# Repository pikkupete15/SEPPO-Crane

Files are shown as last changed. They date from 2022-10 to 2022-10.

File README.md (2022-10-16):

# SEPPO-Crane
Aalto-yliopiston tuotesuunnittelukurssin I/2022 ryhmän 2 prototyypin repo. 

<p>Slave kansio - Arduino koodi slave-saksimoduulille</p>
<p>Master kanstio - Arduino koodi master-saksimoduulille</p>
<p>Ohjain kansio - Processing koodi WiFi-ohjaukselle</p>
<p>Elektroniikka - kytkentäkaaviot, diagrammit, osaluettelot, GRBR-tiedostot, levyjen kuvat</p>



Watch the video (https://www.youtube.com/watch?v=MJLLgqbMfsc)

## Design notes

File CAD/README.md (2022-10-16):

CAD: Fusion 360

viewer; https://viewer.autodesk.com/

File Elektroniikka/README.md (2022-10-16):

Täältä löytyy kytkentäkaaviot, BOM, sekä levyjen GRBR-tiedostot. Kaikki levyt suunniteltu jyrsittäväksi yksipuoleisesta 1.6mm pertinax-levystä. 
Folion paksuus 35µm 

Slave- ja Master-laitteiden levyt ovat identtisiä. Ohjelmalla valitaan joko Slave- tai Master-moodi.


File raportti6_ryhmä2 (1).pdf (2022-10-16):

Aalto-yliopisto Insinööritieteiden korkeakoulu

KJR-C2005 Tuotesuunnittelu

Ryhmä: 2. | Päivämäärä: 16.10.2022
Harjoitus: | Viikkoraportti 6
Otsikko: | Loppuraportti ja Gaala

Tekijät:

| Nimi | Opiskelijanr. | PJ vko
1 | Joonatan Rimpiläinen | 790572 | 1
2 | Niko Kuusisto | 1017131 | 2
3 | Petteri Haverinen | 910064 | 3
4 | Aaro Uitto | 910417 | 4

# Tiivistelmä

Tässä ryhmän 2 tuotesuunnittelukurssin (KJR-C2005) loppuraportissa on kerättynä aiempien viikkoraporttien (1–5) keskeiset asiat. Raportissa esitellään ryhmätyönä toteutetun tuotesuunnitteluprosessin eri vaiheet ja niiden lopputulemat, sekä sen kautta valittu ratkaisuvaihtoehto. Valinnan jälkeen ratkaisuvaihtoehtoa kehitettiin ja siitä laadittiin havainnemalli gaalatilaisuutta varten.

Tuotesuunnittelukurssi toteutettiin yhteistyössä Konecranesin kanssa, joka määritteli tuotesuunnitteluprosessin aiheen. Tehtävänantona oli toteuttaa kuorman nosto- /siirtotapahtuma tehdashallissa. Raportissa esiteltyjen järjestelmällisien suunnittelu- ja ideointimenetelmien jälkeen tuotesuunnitteluprosessin tulokseksi muodostui saksimekanismeja hyödyntävä nosturi, joka ei tarvitse tehdashallilta tukevaa seinärakennetta, eikä kiinteää asennusta.

# Johdanto

Teollisissa nostureissa hyvin tyypillinen ratkaisu on jykevä pääkannatin, joka kulkee pitkittäissuunnassa hallin seinien yläosassa olevilla kiskoilla. Pääkannattimen päällä puolestaan ovat toiset kiskot, joiden päällä vaijerinostinkoneisto pääsee kulkemaan. Tämän ns. siltanosturin ehdoton vahvuus on kustannustehokkuuden ja toimintavarmuuden yhdistelmä. Perinteisellä siltanosturilla on myös merkittäviä rajoituksia. Esimerkiksi enimmäisnostokuorma ei riipu pelkästään itse nosturin lujuudesta, vaan myös tehdashallin seinämien kantokyvystä. Siltanosturit voivat myös tilanteesta riippuen hankalia asentaa ja huoltaa, etenkin jos tehdashallin alkuperäisen rakennuksen yhteydessä siltanosturin asennusmahdollisuutta ei ole huomioitu.

Ryhmänä koimme, että siltanosturille ominaiset käyttötilanteet voivatkin olla hyvin suppeita. Kehittyvän teollisuuden maissa olevissa tuotantohalleissa ei ole välttämättä tarpeeksi vahvoja tukirakenteita perinteisen siltanosturin mahdollistamiseksi, mikä hankaloittaa tai jopa estää raskaan laitteiston sijoittamista tai siirtämistä hallin sisällä. Toinen esimerkki voisi olla vaikka erilaiset messuhallit, kuten telttahallit, joissa raskaan kaluston liikkuminen on haastavaa.

Ratkaisumme avulla pyrimme tutkimaan modulaarisempia ja käytännöllisempiä nosturimalleja juuri näihin joustavuutta vaativiin tilanteisiin.

# Menetelmät

Taustatutkimus – Taustatutkimus on jokaisen tuotesuunnitteluhankkeen kannalta yksi tärkeimmistä vaiheista. Tarvittava ratkaisu voi jo olla olemassa, siihen voi kohdistua tiukkoja laki/standardirajoituksia tai tuotteelle ei ole vielä olemassa markkinaa, jolloin tuotteen suunnittelua ei kannatta toteuttaa. Olemassa olevista ratkaisuista voi myös saada inspiraatiota niitä yhdistelemällä tai muokkaamalla.

Tuotesuunnittelutyön tehtävänannon jälkeen teimme laajan taustatutkimuksen, jolla kartoitimme jo olemassa olevia nosturiratkaisuja, niin kirjallisesti kun paikan päällä tutustumalla. Havaitsimme, että tehdashallissa käytettävät nosturit ovat olleet jo lähes 100 vuotta hyvin samanlaisia. Niitä sitovat tiukat ja yksityiskohtaiset standardit, jotka melko suoraan määrittävät, minkälainen nosturin tulee olla.

Vaatimuslista – Vaatimuslista on jokainen hankkeen yksi tärkeimmistä dokumenteista, sillä siihen määritetään ratkaisulta edellytettävät speksit, kuten sen geometria, energianmuoto tai kustannukset, jonka pohjalta varsinainen suunnittelutyö alkaa.

Vaatimuslistaa varten haastattelimme Konecranesin edustajaa Ari Bertulaa luentojen yhteydessä. Vaatimuslistamme piti sisällään 16 erilaista päätunnusta, kuten kinematiikka, voimat, turvallisuus, joihin määriteltiin tarkasti hankkeen toteutuksen kannalta oleelliset asiat.

Abstrahointi – Abstrahointi on menetelmä, jolla saadaan vaatimuslistan oleelliset asiat esille analysoimalla erilaisten toimintojen riippuvuuksia. Abstrahointi pitää sisällään 5 askelta, jotka ohjaavat kriittisesti karsimaan ja muokkaamaan vaatimuslistaa kohti todellista tarvetta.

Abstrahoimme vaatimuslistamme ensin karsimalla kaikki toiveet sekä sellaiset vaatimukset, jotka eivät välittömästi koskeneet toimintaa tai oleellisia ehtoja. Tämän jälkeen jäljelle jääneet määrälliset toteamukset muutettiin laadullisiksi sekä ne supistettiin oleelliseen pitäytyviksi lausumiksi. Jäljelle jääneet vaatimukset lavennettiin yleisemmälle tasolle, joista lopulla muodostettiin ongelma ratkaisuun nähden neutraalisti. Abstrahointiprosessimme lopputulos oli ”Kuorman nostaminen ja siirtäminen tehdashallissa”.

Kokonaistoimintojen jako osiin – Abstrahoinnin tuloksena saadaan ratkaisuun nähden neutraali kokonaistoiminto. Kokonaistoiminto jaetaan pienempiin osatoimintoihin, joka mahdollistaa niiden yksittäisen tarkastelemisen. Osatoimintoihin jako voidaan suorittaa tarkastelemalla kokonaistoiminnon aiheuttamaa muutosta vertaamalla aineen, energian ja signaalin muutosta ennen kokonaistoimintoa ja sen jälkeen.

Pilkoimme kokonaistoiminnon aluksi karkeasti osatoimintoihin ”kuorman nostaminen”, ”kuorman siirtäminen” ja ”kuorman laskeminen”. Jotka tämän jälkeen uudelleen ositimme pienemmiksi kokonaisuuksiksi sisältäen esimerkiksi ”kiinnityksen nostettavaan massaan”, ”voimien välitys hallin rakenteisiin” ja ”nostoliikkeen pysäytys ja lukitus”.

”635” – menetelmä - “635” on ideointimenetelmä, jossa 6 ihmistä ottaa oman tyhjän paperin ja kirjaa sille 3 ideaa ratkaisuksi. Paperi kierrätetään jokaisen ryhmäläisen kautta, niin että jokaisella on 5 minuuttia aikaa jatkojalostaa ja täydentää kyseisen paperin kolmea ratkaisua. Tällä menetelmä saadaan nopeasti erilaista 18 ratkaisuvaihtoehtoa rakennettua.

Käytimme soveltavasti ”635” -menetelmää, sillä ryhmässämme oli vain 4 jäsentä. Saimme menetelmää käyttäen yhteensä 12 ratkaisuvaihtoehtoa, joista muutama olivat hyvin samankaltaisia keskenään. Ratkaisuvaihtoehdoiksi muodostui esimerkiksi ”vaijerinosturi”, jossa 4 erillistä köysinosturia asennetaan tehdashallin kulmiin ja vaijereiden päät niputettaisiin yhteen jonkin pannan avulla.

Aivoriihi - Aivoriihi on ideointimenetelmä, jossa määrä korvaa laadun. Taustalla onkin nimenomaan ajatus, että määrä tuo laatua. Tässä menetelmässä voi heittää huolettomasti hyvinkin epätavallisia ideoita, joista voi ajatusten vaihdossa jalostua toimivia ratkaisuja.

Kun olimme suorittaneet “635”-ideointimenetelmän ja käyneet yhdessä syntyneet ratkaisuvaihtoehdot lävitse, aloimme luonnostaan itse toteuttamaan aivoriihiä ratkaisujen synnyttäneen keskustelun ansiosta. Aivoriihen tuottamia hahmotelmia piirreltiin yhdessä tyhjän luentosalin liitutaululle, joista otettiin valokuvat talteen. Käydystä aivoriihistä syntyi ensimmäinen kipinä lopulliseen toteutukseemme.

Morfologinen laatikko – Morfologiseen laatikkoon listataan jaettujen osatoimintojen mahdolliset ratkaisuvaihtoehdot ja niitä yhdistelemällä eri tavoin saadaan liuta kokonaisratkaisuvaihtoehtoja. Osittaisratkaisuvaihtoehtojen yhdistely voi olla joko satunnaista, tai se voi perustua esimerkiksi siihen, kuinka hyvin eri vaihtoehdot täydentävät toisiaan ja siten sopivat yhteen.

Ratkaisuvaihtoehtojen arvosteleminen painotetuilla kriteereillä

Osittaisratkaisuista kootut kokonaisratkaisuvaihtoehdot arvostellaan esimerkiksi asteikolla 0-10 eri päätunnusten mukaisesti. Tyypillisiä päätunnuksia voivat olla esimerkiksi turvallisuus, ergonomia, valmistus, asennus, kuljetus, käyttö, kunnossapito, kierrätys sekä kustannukset. Jokaiselle päätunnukselle määritetään jokin painotus kokonaisarvioinnissa, jotta tärkeiksi koetut ominaisuudet omaaville ratkaisuille tulee enemmän näkyvyyttä

# Tulokset

Ratkaisun toiminnallinen pienoismalli saatiin toteutettua ja demonstroitua tuotesuunnittelukurssin gaalassa 11.10.2022.

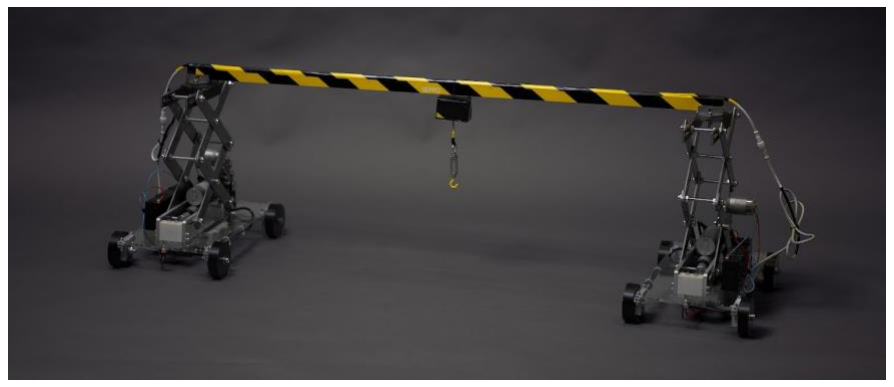
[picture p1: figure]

KUVA 1 VALMIS PROTOTYYPPI NOSTOASENNOSSA

Laitteen prototyypille annettiin nimitys SEPPO. Nimen etymologia tulee Seppo Ilmarisesta sekä ryhmän jäsenen isoisän nimestä.

Laite suunniteltiin Fusion-360 CAD-ohjelmalla ja valmistettiin Aalto Design Factory:n tiloissa. Yhteensä koneistettuja, vesileikattuja, sorvattuja sekä 3D-tulostettuja osia oli 61. Saksipareja päädyttiin tekemään 2 kappaletta. Lisäämällä tai vähentämällä saksipareja, saadaan nostokorkeutta säädettyä standardiosilla. Nostomekanismi on valmis moduuli, joka kulkee pääkannattimella (kuva 1. Musta laatikko pääkannattimen keskellä), joten sitä ei mallinnettu eikä sähköistetty.

Prototyyppi rakentuu kahdesta saksimoduulista, eli pääkannatinta kannattelevista pyörillä kulkevista rakenteista. Molemmat rakenteet sisältävät sähkömoottorin ajamiseen sekä käyttölaitteen saksimekanismin nostamiselle/laskemiselle. Toinen moduuleista on Master-laite, eli sen kautta kulkevat komennot ohjaavat toista moduulia, joka on Slave-laite. Saksimoduulit keskustelevat keskenään UART-väylän kautta. Lisäksi molemmissa moduuleissa on langallinen manuaaliohjaus, eli neljä kytkintä, jotka mahdollistavat moduulin liikkeen eteen-taakse sekä saksimekanismin nostamisen ja laskemisen. Ohjausmekanismia eturenkaille ei prototyyppiin toteutettu.

Elektroniikka kiinnitettiin laitteen pohjaan. Ohjauslevy koteloitiin, mutta H-silta jätettiin avoimeksi kuumenemisen ehkäisemiseksi. Toiminnoista löytyy demovideo (liite 2).

Prototyyppi toimi odotusten mukaisesti – halutut toiminnot saatiin sisäistettyä prototyyppiin. Laitteen toiminta on seuraavanlainen:

1. Saksimoduulit (kuva 1. vasen ja oikea, pääkannattimella yhdistetyt rakenteet) ajetaan käytettävään tilaan pääkannatin käännettynä toisen moduulin suuntaisesti.
2. Toinen saksimoduuli, joka ei kuljeta pääkannatinta ajetaan pääkannatinta kannattavan moduulin viereen.
3. Pääkannattimen satulan kääntölukitus poistetaan ja se käännetään toisen moduulin satulaan kiinni ja lukitaan pultilla (kuva 3 & 4, pääkannattimen alla oleva osa).
4. Toinen moduuli ajetaan etuviistoon ja peruutetaan samalle tasalle, pääkannattimen etäisyyden päähän paikallaan olevasta saksimoduulista.
5. Pyörivät satulamekanismit lukitaan paikalleen.
6. Pääkannatin nostetaan käyttökorkeuteen saksimekanismilla (kuva 4).
7. Laite käyttövalmis (kuva 1).

Molemmat saksimoduulit toimivat itsenäisesti manuaalisella ohjauksella, kun pääkannatinta pitkin kulkeva datalinja ei ole yhdistetty. Kun datalinja yhdistää moduulit, poistuu Slave-moduulin manuaaliohjaus käytöstä, mikä mahdollistaa synkronoidun ohjauksen Master-moduulilta. Manuaaliohjauksen lisäksi laite toimii myös WiFi:n kautta kauko-ohjauksella.

Sulautettu ohjelmisto tehtiin käyttämällä Arduino-kieltä, joka perustuu C ja C++ kieliin. Kaukoohjauksessa käytetty sovellus tehtiin käyttämällä Processing-kieltä. Processing perustuu Javakieleen. WiFi-ohjaus perustuu laitteen ylläpitämään TCP-serveriin, mihin ohjaussovellus liittyy clienttinä lähettäen komentoja, jotka ovat identtisiä UART-komentojen kanssa. Tämä mahdollisti saman string parserin käytön sekä UART-, että WiFi-ohjaukselle.

Kytkentäkaaviot, piirilevyt, koodi sekä CAD-tiedostot löytyvät julkisesta github-reposta (liite 1).

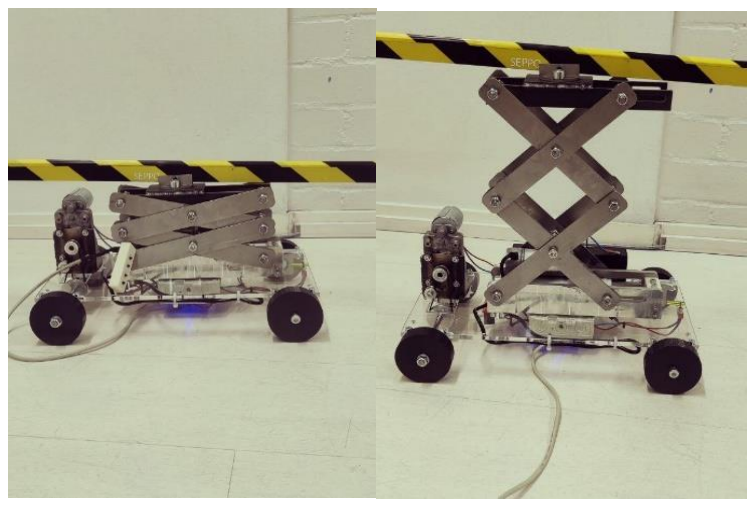
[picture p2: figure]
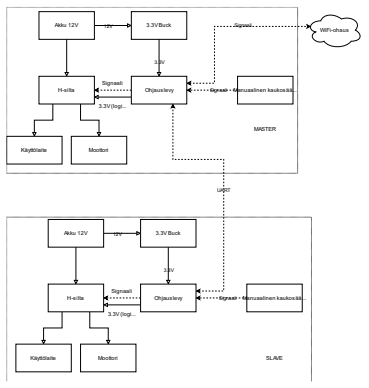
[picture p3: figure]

KUVA 2 ELEKTRONIIKAN OSATOIMINNOT | KUVA 3&4 SAKSIMODUULI ALA- (VAS.) SEKÄ YLÄ-ASENNOSSA (OIK.)

# Pohdinta

Tuotesuunnitteluprosessin tulosten perusteella voidaan sanoa, että uudenlaisen nosturigeometrian luominen on sekä mahdollista että myöskin tarpeellista. Ratkaisumme tuottaa joustavamman ratkaisun epätavallisiin tilanteisiin, joihin perinteinen nosturi ei välttämättä soveltuisi. Lisäksi hinta voi olla perinteistä ratkaisua alempi varsinkin halleissa, joihin ei ole mahdollista asentaa siltanosturia ilman mittavaa remonttia.

Saksinosturi-siltanosturi-hybridiä voitaisiin teollisuussovellusten lisäksi hyödyntää esimerkiksi messuhalleissa, liikkuvuutta ja joustavuutta vaativissa esittelytiloissa, sekä pienillä rakennustyömailla, kuten yksittäisten omakotitalojen rakennuksessa.

Yksittäisen saksinostinelementin sivuttaissuuntaista vakautta ja jykevyyttä olisi syytä käsitellä mahdollisen jatkokehityksen yhteydessä. Saksinostimen lukitusratkaisuja ja niiden suorituskykyä emme käsitelleet tässä prosessissa juurikaan, mikä avaa oven lisätutkimuksille. Lisäksi yksittäiselle nostinelementille voi olla saksinostimen lisäksi myös muita joko varmempia tai kustannustehokkaampia malleja.

Myös pääkannattimeen liittyviä vaihtoehtoja on syytä tutkia, eritoten pääkannattimen ja nostinelementin liitäntää koskien. Pääkannattimen modulaarisuuden ja asennuksen yksinkertaistaminen erilaisten lisäratkaisujen avulla voisi olla myös hyödyllistä

# Tuntikirjanpito

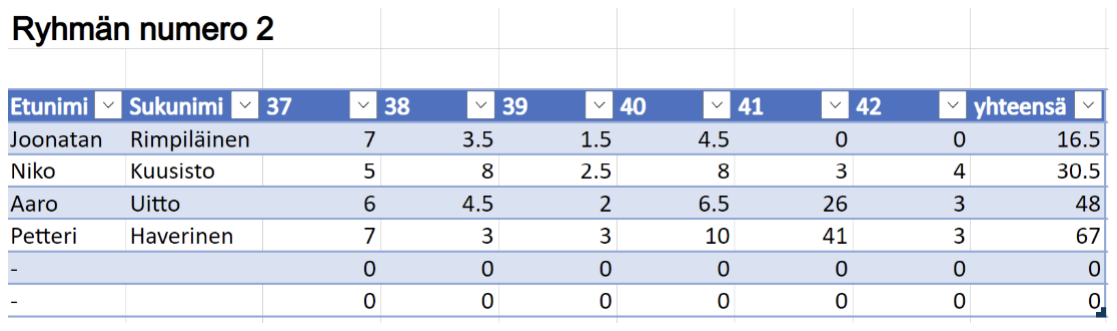
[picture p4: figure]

# Vertaisarviointi

Ryhmän jäsenten mielestä suoriutuminen kurssista oli pääasiassa sujuvaa. Raporteissa onnistuimme parista puutteellisuudesta huolimatta hyvin, ja prosessia seurasimme tarkasti. Havainnemallin toteutukseen olemme hyvin tyytyväisiä, ja prosessin tuottama ratkaisu oli mielestämme looginen. Näiden seikkojen nojalla arvioimme suorituksemme tason riittävän arvosanaan 5.

Tuntikirjanpidossa näkyvät Petteri Haverisen ja Aaro Uiton korkeammat tuntimäärät ovat seurausta prototyypin rakennukseen kuluneesta suuresta ajasta. Jos tämä aika jätettäisiin huomiotta, olisivat tuntimäärät ryhmän jäsenten välillä huomattavasti lähempänä toisiaan.

# Palaute

Kurssin aikana saatu ohjeistus ja tuki oli kattavaa, ja opitun prosessin merkitys ja yksityiskohdat tulivat selkeäksi tavalla, joka on helppo muistaa. Ainoana negatiivisena asiana olisi suunnitteluprosessin aihe, joka oli hieman rajallinen/haastava, mutta tämä ei ole tietenkään kurssin järjestäjien hallinnassa.

Viittaukset ja liitteet

1) Github: https://github.com/pikkupete15/SEPPO-Crane
2) Demonstraatiovideo: https://www.youtube.com/watch?v=MJLLgqbMfsc

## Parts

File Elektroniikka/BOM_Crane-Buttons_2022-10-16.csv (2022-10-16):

ID | Name | Designator | Footprint | Quantity | Manufacturer Part | Manufacturer | Supplier | Supplier Part | Price
1 | HDR-F-2.54_1x5 | H1 | HDR-F-2.54_1X5 | 1 |  |  | LCSC | C50950 | 0.064
2 | K4-6×6_SMD | KEY1,KEY2,KEY3,KEY4 | KEY-SMD_4P-L6.0-W6.0-P3.90-LS10.0 | 4 | K2-6639SP-D4SC-04 | 韩国韩荣 | LCSC | C191626 | 0.052

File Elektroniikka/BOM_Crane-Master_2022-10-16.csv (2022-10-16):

ID | Name | Designator | Footprint | Quantity | Manufacturer Part | Manufacturer | Supplier | Supplier Part | Price
1 | HDR-F-2.54_1x5 | H1 | HDR-F-2.54_1X5 | 1 |  |  | LCSC | C50950 | 0.064
2 | CONN-TH_2P-P5.00 | P1,P2,P3,P5 | CONN-TH_2P-P5.00 | 4 |  |  | LCSC
3 | CONN-TH_3P-P5.00 | P4 | CONN-TH_3P-P5.00 | 1 |  |  | LCSC
4 | 1k | R1,R2,R3,R4 | R1206 | 4
5 | Buck-module | U1 | BUCK-MODULE | 1 |  |  |  | https://www.amazon.com/4-75-23V-1-17V-DC-DC-Converter-Module/dp/B00NJCAI7G
6 | WEMOS-D1-MINI | WEMOS1 | WEMOS-D1-MINI | 1

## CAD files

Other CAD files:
CAD/Tuotesuunnitteluprojekti v25.f3d

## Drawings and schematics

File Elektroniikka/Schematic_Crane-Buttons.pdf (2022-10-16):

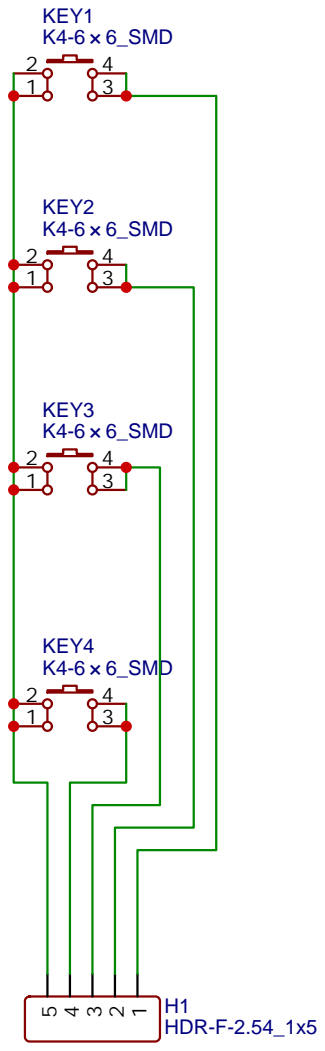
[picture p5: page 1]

Drawn By: Petteri Haverinen

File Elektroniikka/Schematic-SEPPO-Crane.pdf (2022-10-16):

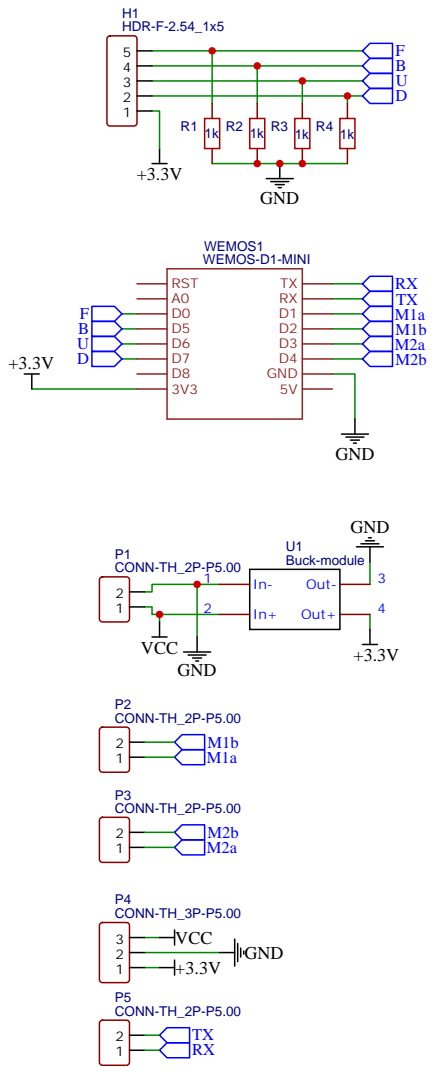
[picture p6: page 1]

Drawn By: Petteri Haverinen

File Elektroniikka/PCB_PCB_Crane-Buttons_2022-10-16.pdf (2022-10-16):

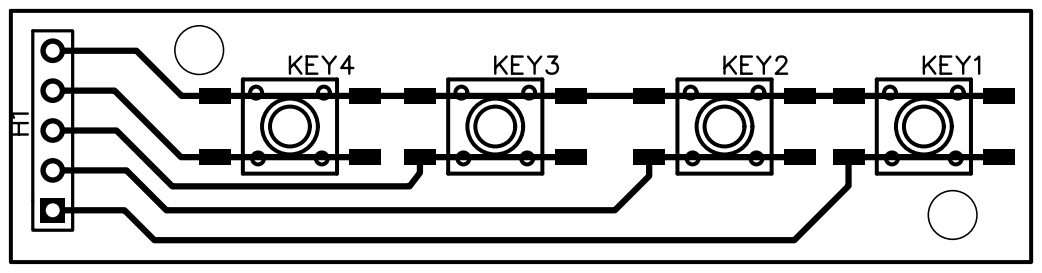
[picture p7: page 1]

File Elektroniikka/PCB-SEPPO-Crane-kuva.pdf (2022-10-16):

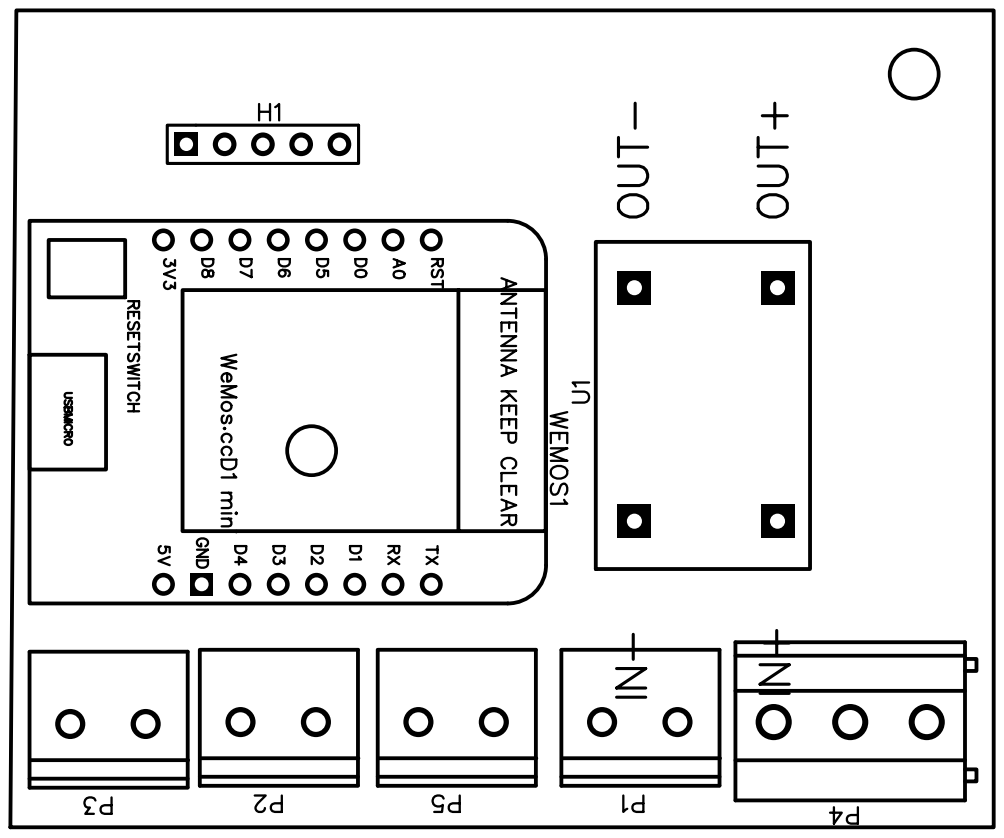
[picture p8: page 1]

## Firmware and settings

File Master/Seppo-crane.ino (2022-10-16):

#include <ESP8266WiFi.h>
#include <ESP8266WebServer.h>

const char* ssid = "SEPPO";
const char* pass = "Tuotesuunnittelu";


WiFiServer server(8080);

// Device Local IP
IPAddress IP(192, 168, 1, 184);
// Device GatewaY
IPAddress gateway(192, 168, 1, 1);
// Subnet mask
IPAddress subnet(255, 255, 0, 0);

#define FWD   D1
#define BWD   D2
#define UP    D3
#define DOWN  D4

#define input1  D0
#define input2  D5
#define input3  D6
#define input4  D7

#define master true

int Up = 0;
int Down = 0;
int Fwd = 0;
int Bwd = 0;
int inputInts[8];

void setup() {


  WiFi.disconnect();

  WiFi.mode(WIFI_AP_STA);

  if (!WiFi.softAPConfig(IP, gateway, subnet)) {
    Serial.println("STA Failed to configure");
  }

  WiFi.softAP(ssid);

  WiFi.softAP(ssid);

  Serial.print("CONNECTED! IP Address: ");
  Serial.println(WiFi.softAPIP());

  server.begin();


  pinMode(FWD, OUTPUT);
  pinMode(BWD, OUTPUT);
  pinMode(UP, OUTPUT);
  pinMode(DOWN, OUTPUT);

  pinMode(input1, INPUT);
  pinMode(input2, INPUT);
  pinMode(input3, INPUT);
  pinMode(input4, INPUT);

  Serial.begin(9600);

}

void loop() {

  WiFiClient client = server.available();

  while (client.connected()) {
    if (client.available()) {
      String input = client.readStringUntil('\n');
      input.trim();
      //Serial.println(input);

      int valueIndex = 0;
      int intIndex = 0;
      for (int i = 0; i < input.length(); i++) {
        if (input.charAt(i) == ';') {
          String tempString =  input.substring(valueIndex, i);
          inputInts[intIndex] = tempString.toInt();
          intIndex++;
          valueIndex = i + 1;
          //Serial.println(tempString);
        }
      }
      Fwd = inputInts[0];
      Bwd = inputInts[1];
      Up = inputInts[2];
      Down = inputInts[3];

      if (Fwd == 1) {
        digitalWrite(FWD, HIGH);
        digitalWrite(BWD, LOW);
        digitalWrite(UP, LOW);
        digitalWrite(DOWN, LOW);
        Serial.println("1;0;0;0;");
      }

      else if (Bwd == 1) {
        digitalWrite(FWD, LOW);
        digitalWrite(BWD, HIGH);
        digitalWrite(UP, LOW);
        digitalWrite(DOWN, LOW);
        Serial.println("0;1;0;0;");
      }

      else if (Up == 1) {
        digitalWrite(FWD, LOW);
        digitalWrite(BWD, LOW);
        digitalWrite(UP, HIGH);
        digitalWrite(DOWN, LOW);
        Serial.println("0;0;1;0;");
      }

      else if (Down == 1) {
        digitalWrite(FWD, LOW);
        digitalWrite(BWD, LOW);
        digitalWrite(UP, LOW);
        digitalWrite(DOWN, HIGH);
        Serial.println("0;0;0;1;");
      }

      else {
      digitalWrite(FWD, 0);
      digitalWrite(BWD, 0);
      digitalWrite(UP, 0);
      digitalWrite(DOWN, 0);
      Serial.println("0;0;0;0;");
    }



      Serial.println((String)Fwd + ";" + Bwd + ";" + Up + ";" + Down + ";");

      Fwd = 0;
      Bwd = 0;
      Up = 0;
      Down = 0;


    }
    
  }

  /*
    if (Serial.available()) {
    String input = Serial.readStringUntil('\n');
    Serial.println(input);

    int valueIndex = 0;
    int intIndex = 0;
    for (int i = 0; i < input.length(); i++) {
      if (input.charAt(i) == ';') {
        String tempString =  input.substring(valueIndex, i);
        inputInts[intIndex] = tempString.toInt();
        intIndex++;
        valueIndex = i + 1;
        Serial.println(tempString);
      }
    }
    Fwd = inputInts[0];
    Bwd = inputInts[1];
    Up = inputInts[2];
    Down = inputInts[3];

    digitalWrite(FWD, Fwd);
    digitalWrite(BWD, Bwd);
    digitalWrite(UP, Up);
    digitalWrite(DOWN, Down);

    Fwd = 0;
    Bwd = 0;
    Up = 0;
    Down = 0;

    }
    else {
    digitalWrite(FWD, 0);
    digitalWrite(BWD, 0);
    digitalWrite(UP, 0);
    digitalWrite(DOWN, 0);
    }
  */

  if (digitalRead(input1) == HIGH && client.connected() == false) {
    digitalWrite(FWD, LOW);
    digitalWrite(BWD, LOW);
    digitalWrite(UP, HIGH);
    digitalWrite(DOWN, LOW);
    Serial.println("0;0;1;0;");
  }

  else if (digitalRead(input2) == HIGH) {
    digitalWrite(FWD, LOW);
    digitalWrite(BWD, LOW);
    digitalWrite(UP, LOW);
    digitalWrite(DOWN, HIGH);
    Serial.println("0;0;0;1;");
  }

  else if (digitalRead(input3) == HIGH) {
    digitalWrite(FWD, HIGH);
    digitalWrite(BWD, LOW);
    digitalWrite(UP, LOW);
    digitalWrite(DOWN, LOW);
    Serial.println("1;0;0;0;");
  }

  else if (digitalRead(input4) == HIGH) {
    digitalWrite(FWD, LOW);
    digitalWrite(BWD, HIGH);
    digitalWrite(UP,  LOW);
    digitalWrite(DOWN, LOW);
    Serial.println("0;1;0;0;");
  }

  else if (digitalRead(input1) == LOW && digitalRead(input2) == LOW && digitalRead(input3) == LOW && digitalRead(input4) == LOW) {
    digitalWrite(FWD, LOW);
    digitalWrite(BWD, LOW);
    digitalWrite(UP, LOW);
    digitalWrite(DOWN, LOW);
    Serial.println("0;0;0;0;");
  }


}

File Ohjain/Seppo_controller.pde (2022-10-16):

import processing.net.*; 

Client Seppo; 
int dataIn; 
String data = "0;0;0;0;";

void setup() { 
  size(200, 200); 
  Seppo = new Client(this, "192.168.1.184", 8080);
} 

void draw() {
  
}


void keyPressed() {
  if (key == 'a' || key == 'A') { //FWD
    data = "1;0;0;0;\n";
  } else if (key == 'd' || key == 'D') { //BWD
    data = "0;1;0;0;\n";
  } else if (key == 'W' || key == 'w') { //UP
  
    data = "0;0;1;0;\n";
  } else if (key == 's' || key == 'S') { //DOWN
    data = "0;0;0;1;\n";
    
  } else {
    data = "0;0;0;0;";
  }
  Seppo.write(data+"\n");
  println(data);
}

void keyReleased(){
  data = "0;0;0;0;";
  Seppo.write(data+"\n");
}

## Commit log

2022-10-16 Master-laitteen Arduino koodi
    Mikrokontrolleri - ESP-D1-mini
2022-10-16 Slave-laitteen koodi
    Mikrokontrolleri: ESP8266-D1-mini
    Arduino - core
2022-10-16 Master-laitteen koodi
    Arduino-core
    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
2022-10-16 Elektroniikan osalista - ohjauslevy
    [BOM_Crane-Master_2022-10-16.csv]
